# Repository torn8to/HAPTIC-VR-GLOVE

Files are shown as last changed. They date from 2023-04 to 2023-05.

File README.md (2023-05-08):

# Variable Haptic Feedback VR Gloves

We present the development of a haptic virtual reality (VR) glove with variable force feedback, electrotactile feedback, and finger tracking using a hall effect linear encoder and closed-loop control. The proposed glove consists of a custom-made linear encoder based on hall effect sensors to measure finger positions, and a closed-loop control system to provide variable force feedback. Additionally, the glove also attempts to incorporate electrotactile feedback to simulate the sensation of touch. Results show that the proposed glove is capable of providing realistic haptic feedback to users. We hope that this capability will improve the users sense of immersion and presence in virtual environments. Or allow for more intuitive control of various robotics systems. Overall, the proposed VR glove can serve as a valuable tool for a wide range of applications, including training simulations, gaming, and teleoperation.

<div id="cad_model" alingment="center">
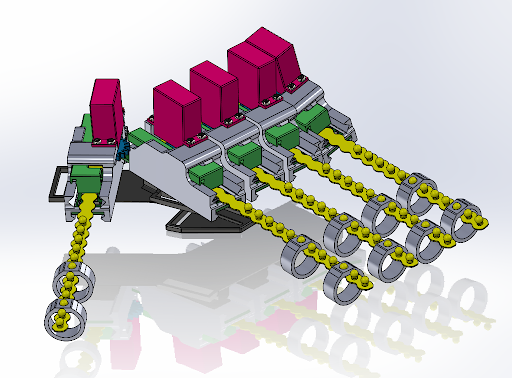
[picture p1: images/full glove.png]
   
</div>

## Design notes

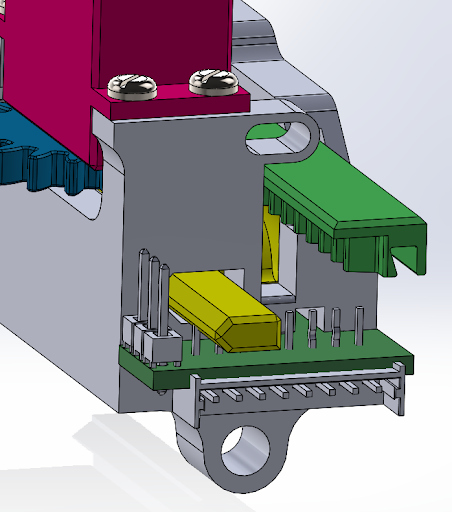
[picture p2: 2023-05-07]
images/back.png

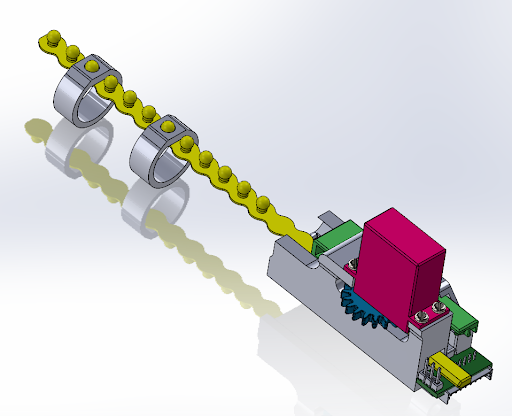
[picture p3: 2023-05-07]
images/full module.png

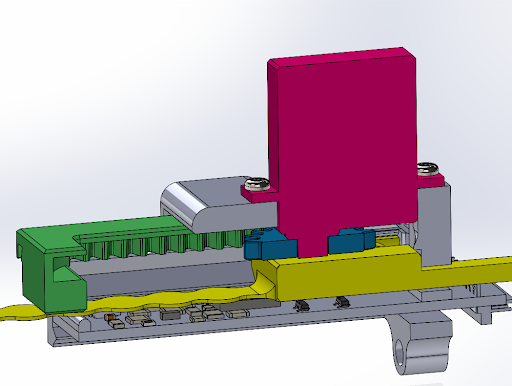
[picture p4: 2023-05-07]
images/cross-section not blocked.png

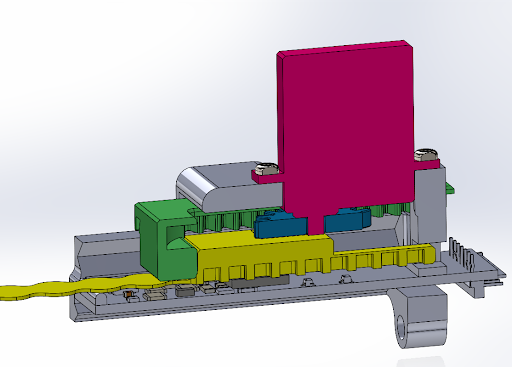
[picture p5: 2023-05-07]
images/cross-section blocked.png

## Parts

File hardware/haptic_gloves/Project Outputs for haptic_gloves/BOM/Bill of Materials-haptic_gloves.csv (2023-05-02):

comment | Designator | Footprint
Spacer, Round, 1/4 Inch O.D., 1/4 Inch Long, #8 Hole, Phenolic
KEYSTONE - 1048 - BATTERY HOLDER, 18650 LI-ION, 2CELL, SMD | B2
100 nf | C1, C3 | 2
330 nf | C2 | 1206_C
10 uf | C4 | 1206_C
1uf | C5, C7, C9, C10, C13 | 0805_C
4.7nf | C6, C8, C11, C12, C14 | 1206_C
 | J1, J2, J3, J4, J5, J6 | .1 1x8
THT Vertical Pin Header WR-PHD, Pitch 2.54 mm, Single Row, 20 pins | P1, P2 | 2.54mm to
Positive Voltage Regulator, 5V, 3-Pin TO-220 | U1 | 1
Fixed Low Drop Positive Voltage Regulator, 3.3V, 3-Pin TO-220 | U2 | 1
analog mux | U3, U9 | ssop-24
SENSOR CURRENT HALL | U4, U5, U6, U7, U8 | 8 soic

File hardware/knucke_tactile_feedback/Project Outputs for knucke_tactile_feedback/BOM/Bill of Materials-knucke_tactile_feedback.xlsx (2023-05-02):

comment | Designator | footprint
1uf | C1 | 0603_C
.1uf | C2, C3 | 0402_C
sMT connector | J2
TSW-103-07-L-S | P2 | .1 X 3
MMBT4403LT1G | Q1 | sot23-3
TNPU1206100RBZEN00 | R1, R2, R4, R5, R6, R8 | 1206_R
100 ohm resistor | R3, R7, R9 | 1210_R
20k resistor | R10 | 0805_R
10k resistor | R11 | 0805_R
10 ohm resistor | R12, R13 | 0805_R
hall effect sensor | U1, U2 | sot-23-3
HX711 | U3 | SOP-16

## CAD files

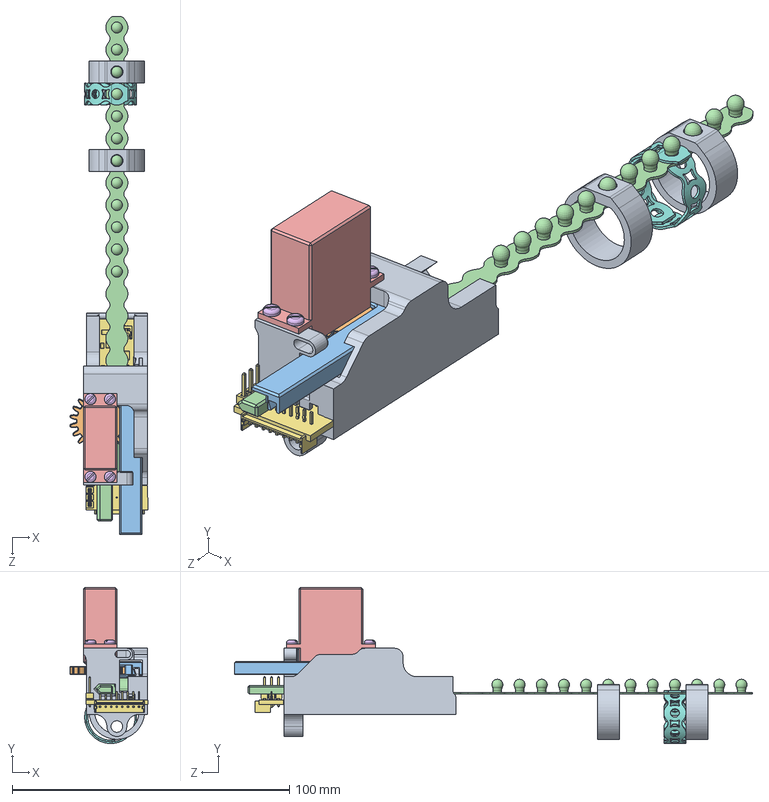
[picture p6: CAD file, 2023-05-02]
hardware/GloveAssembly/FingerModuleAssembly.SLDASM
28.1 x 56.2 x 186.8 mm
Base
ServoGear
ServoRackV2
Slider
AGFRC Micro Servo
pan head tapping screw_am x 4
FINGER_PCB
Ring8 x 2

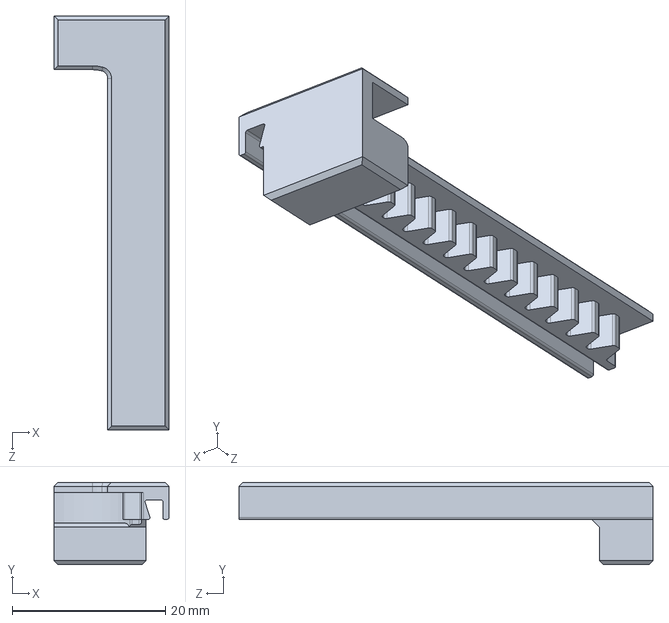
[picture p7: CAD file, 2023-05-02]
hardware/GloveAssembly/ServoRackV2.SLDPRT
15.0 x 10.7 x 54.0 mm

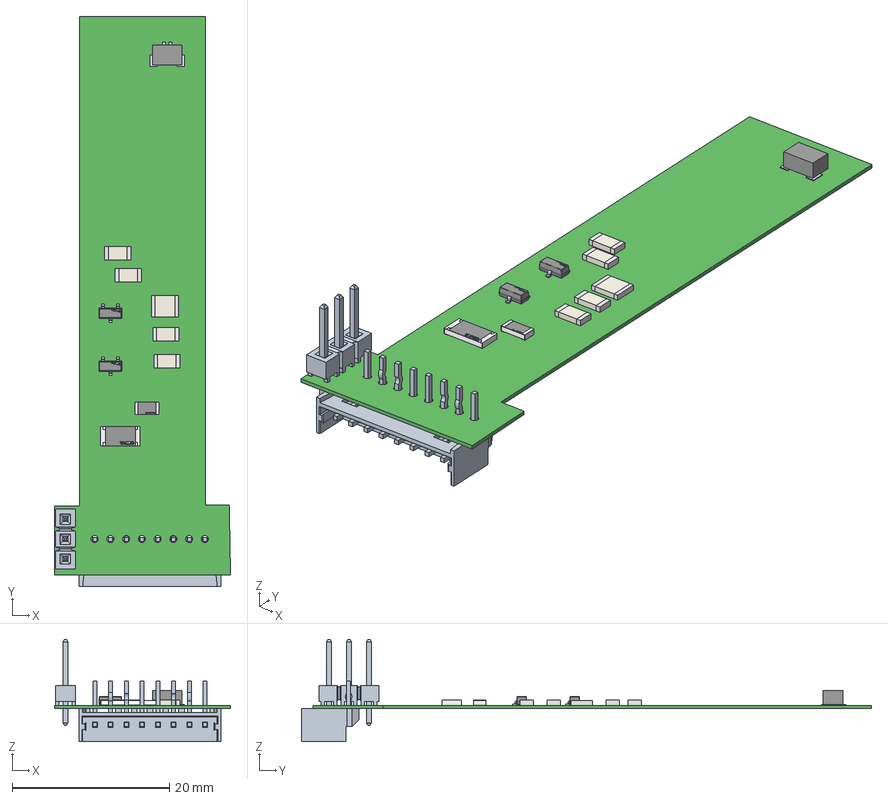
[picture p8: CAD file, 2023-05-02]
hardware/knucke_tactile_feedback/double_halleffect_corrected.step
22.4 x 72.5 x 13.0 mm
RC2010JK-071KL
Yageo
pins x 2
logo x 3
terminals
top
Pins
Extruded x 15
TSW-103-07-X-S

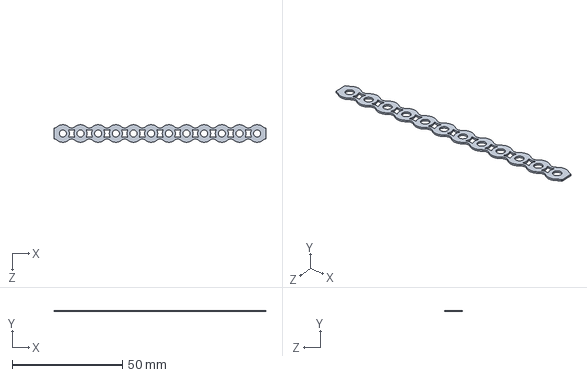
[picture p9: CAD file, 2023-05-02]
hardware/GloveAssembly/AdjustableRing.SLDPRT
96.0 x 0.6 x 8.00 mm

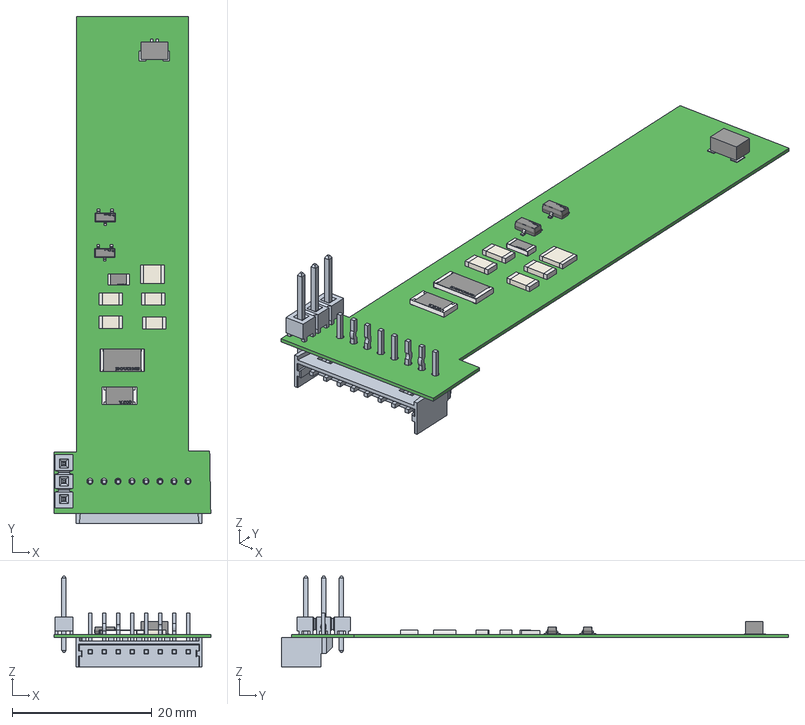
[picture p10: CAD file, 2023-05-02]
hardware/knucke_tactile_feedback/double_hall_effect.step
22.4 x 72.5 x 13.0 mm
RC2010JK-071KL
Yageo
pins x 2
logo x 4
terminals x 2
top x 2
Pins
Extruded x 15
TSW-103-07-X-S

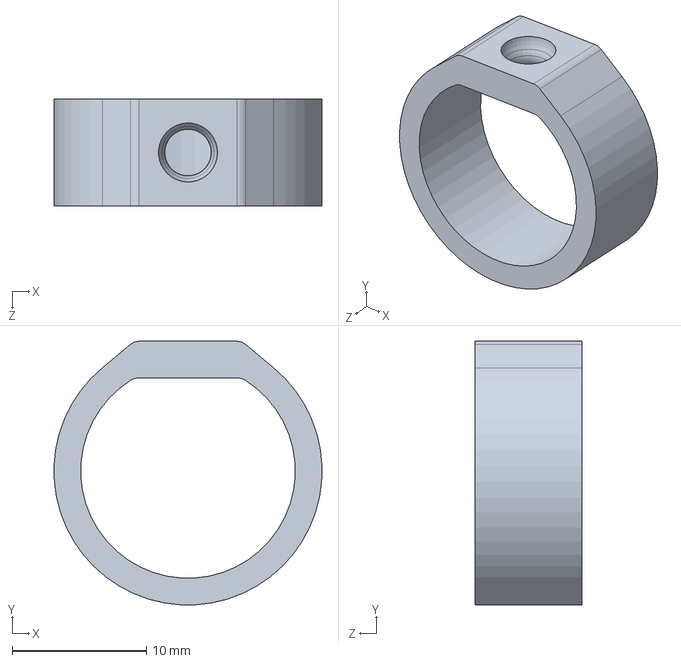
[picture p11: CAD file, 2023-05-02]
hardware/GloveAssembly/Ring8.SLDPRT
20.0 x 19.7 x 8.00 mm

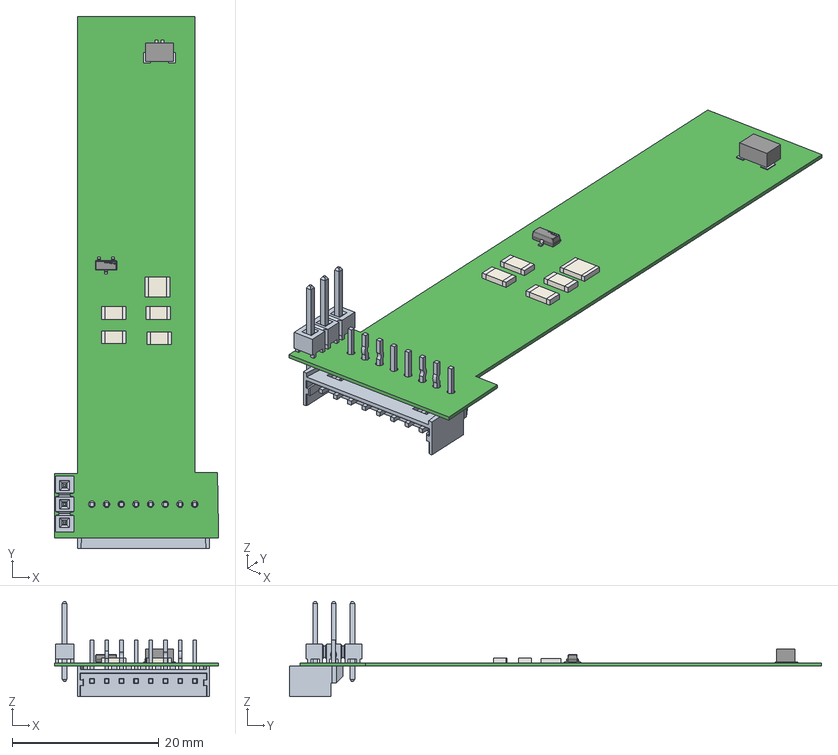
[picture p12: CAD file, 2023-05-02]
hardware/knucke_tactile_feedback/PCB1.step
22.4 x 72.5 x 13.0 mm
Pins
pins
logo
Extruded x 15
TSW-103-07-X-S

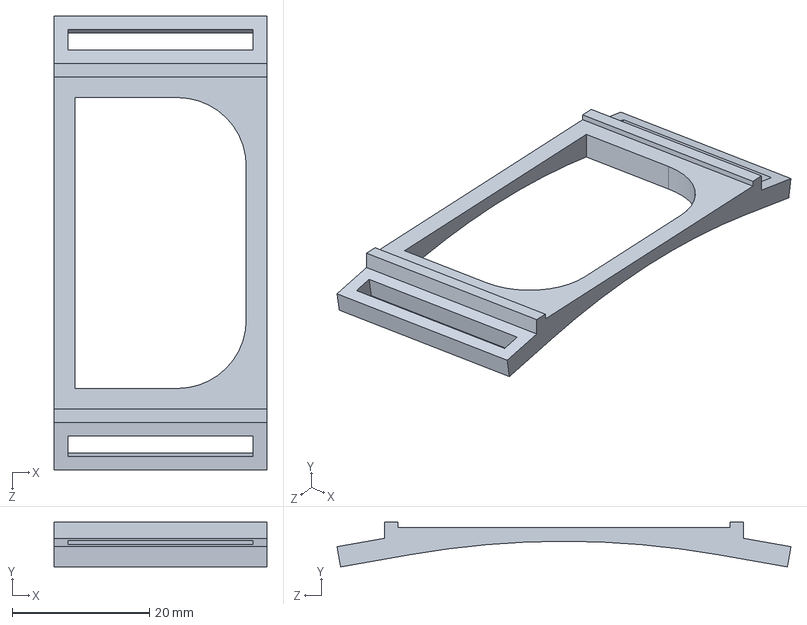
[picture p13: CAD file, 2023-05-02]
hardware/GloveAssembly/ArmBoardMount.SLDPRT
31.0 x 6.54 x 66.2 mm

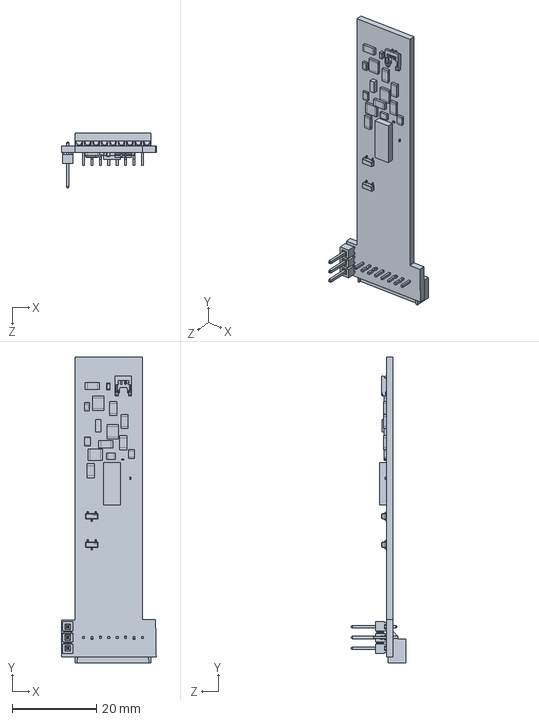
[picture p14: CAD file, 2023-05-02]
hardware/GloveAssembly/FINGER_PCB.SLDPRT
22.4 x 72.5 x 13.0 mm

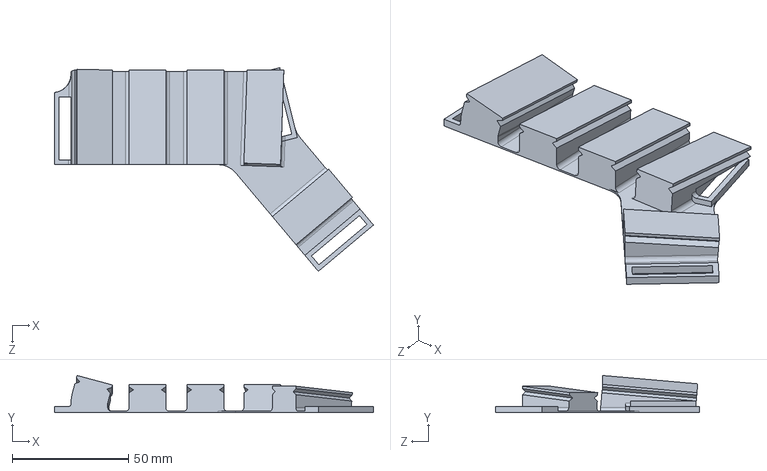
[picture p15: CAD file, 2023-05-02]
hardware/GloveAssembly/HandMount.SLDPRT
137.3 x 16.0 x 87.7 mm

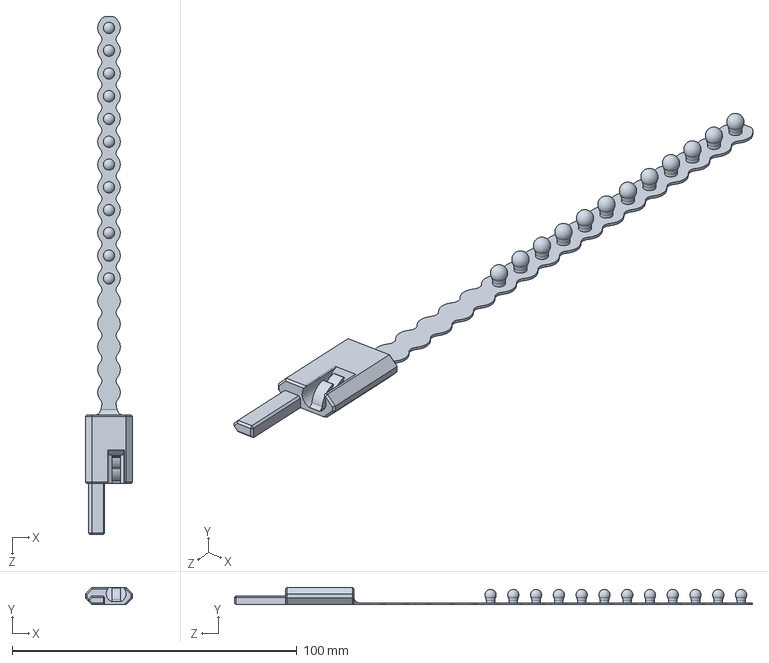
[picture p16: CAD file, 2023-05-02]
hardware/GloveAssembly/Slider.SLDPRT
16.6 x 6.00 x 181.9 mm

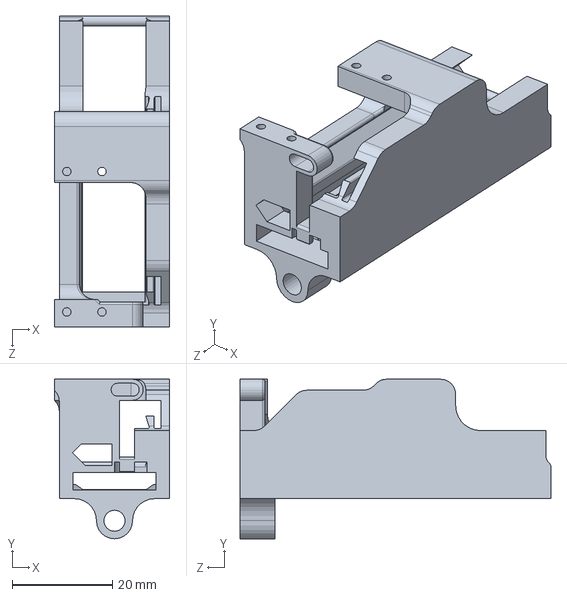
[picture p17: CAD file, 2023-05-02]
hardware/GloveAssembly/Base.SLDPRT
23.0 x 31.8 x 62.0 mm

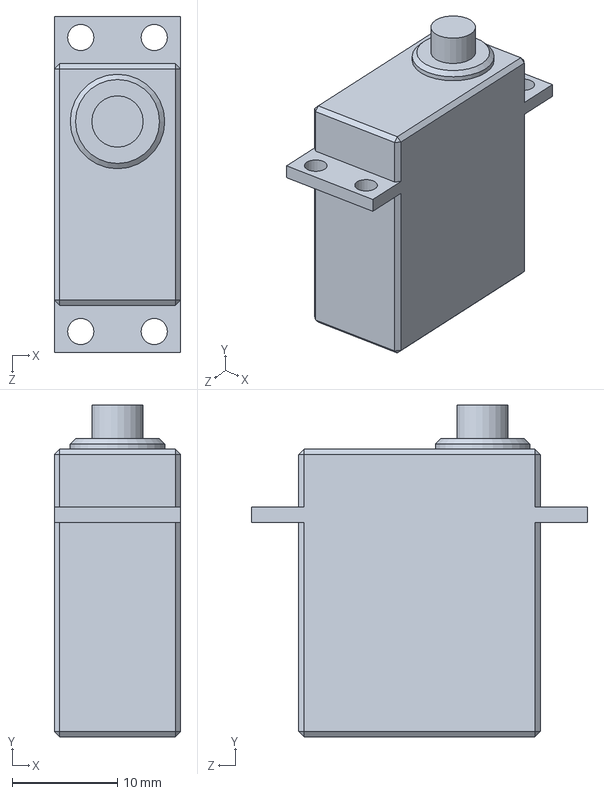
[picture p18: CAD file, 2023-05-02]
hardware/GloveAssembly/AGFRC Micro Servo.SLDPRT
12.0 x 31.6 x 32.0 mm

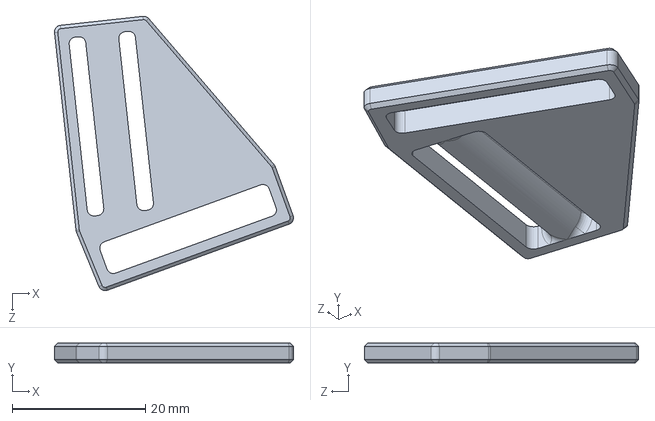
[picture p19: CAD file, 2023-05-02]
hardware/GloveAssembly/FrontHandClip.SLDPRT
35.9 x 3.00 x 41.2 mm

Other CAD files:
hardware/knucke_tactile_feedback/double_halleffect_placcement1.step
hardware/GloveAssembly/MasterSketch.SLDPRT
hardware/GloveAssembly/ServoGear.SLDPRT

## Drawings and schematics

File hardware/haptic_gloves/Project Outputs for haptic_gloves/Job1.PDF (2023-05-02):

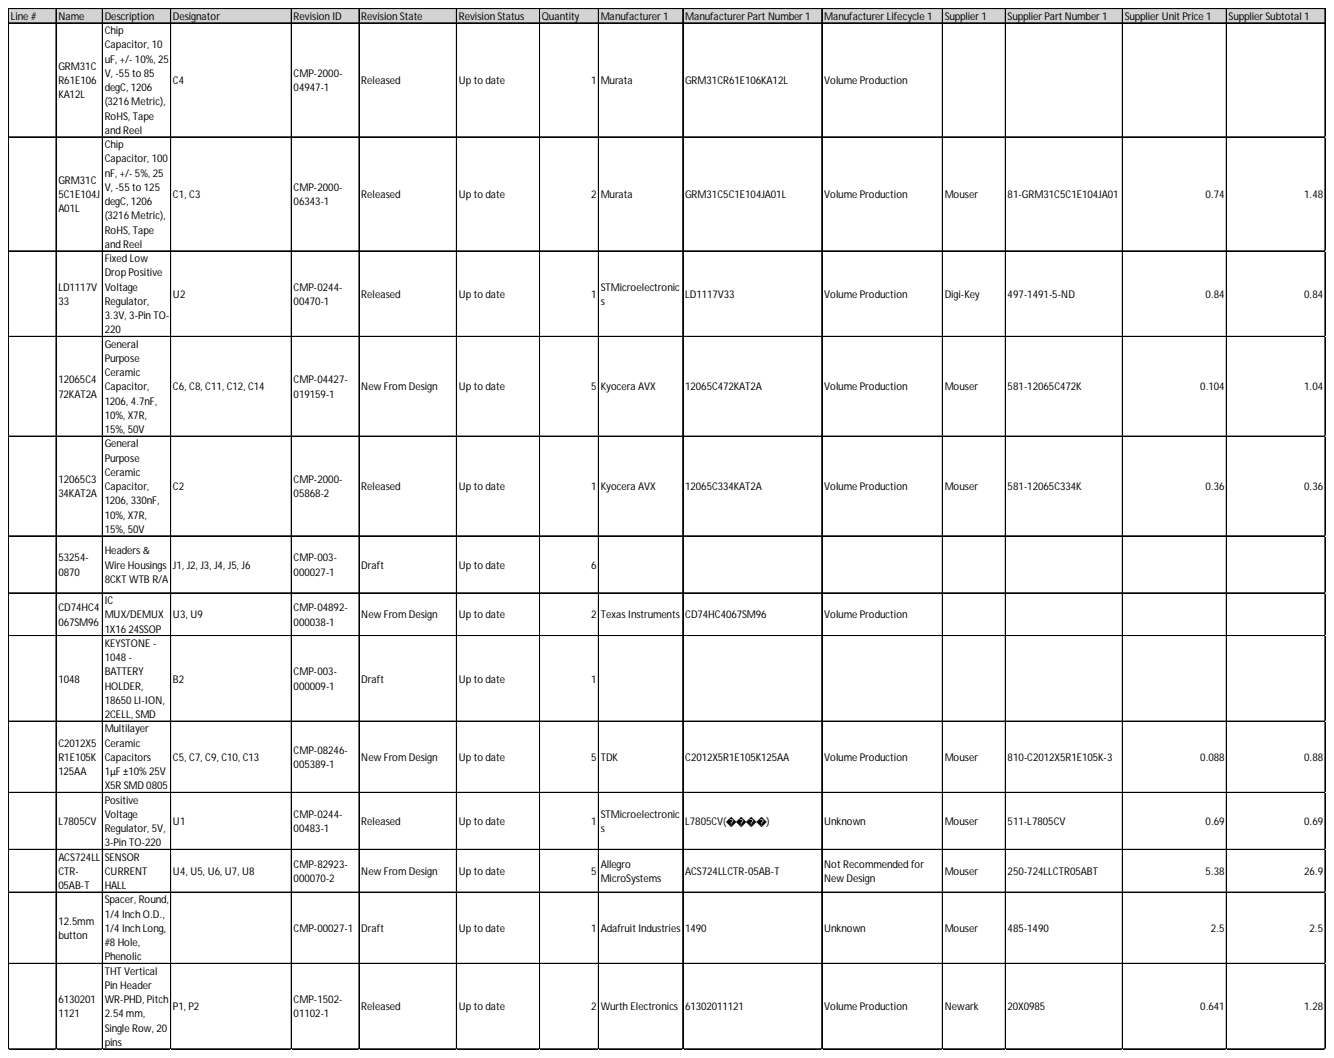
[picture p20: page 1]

Line # | Name | Description | Designator | Revision ID | Revision State | Revision Status | Quantity | Manufacturer 1 | Manufacturer Part Number 1 | Manufacturer Lifecycle 1 | Supplier 1 | Supplier Part Number 1 | Supplier Unit Price 1 | Supplier Subtotal 1

GRM31C R61E106 KA12L | Chip Capacitor, 10 uF, +/- 10%, 25 V, -55 to 85 degC, 1206 (3216 Metric), RoHS, Tape and Reel | C4 | CMP-2000-04947-1 | Released | Up to date | 1 | Murata | GRM31CR61E106KA12L | Volume Production

GRM31C 5C1E104J A01L | Chip Capacitor, 100 nF, +/- 5%, 25 V, -55 to 125 degC, 1206 (3216 Metric), RoHS, Tape and Reel | C1, C3 | CMP-2000-06343-1 | Released | Up to date | 2 Murata | | GRM31C5C1E104JA01L | Volume Production | Mouser | 81-GRM31C5C1E104JA01 | 0.74 | 1.48

LD1117V 33 | Fixed Low Drop Positive Voltage Regulator, 3.3V, 3-Pin TO-220 | U2 | CMP-0244-00470-1 | Released | Up to date | 1 | STMicroelectronic s | LD1117V33 | Volume Production | Digi-Key | 497-1491-5-ND | 0.84 | 0.84

12065C4 72KAT2A | General Purpose Ceramic Capacitor, 1206, 4.7nF, 10%, X7R, 15%, 50V | C6, C8, C11, C12, C14 | CMP-04427-019159-1 | New From Design | Up to date | 5 Kyocera AVX | | 12065C472KAT2A | Volume Production | Mouser | 581-12065C472K | 0.104 | 1.04

12065C3 34KAT2A | General Purpose Ceramic Capacitor, 1206, 330nF, 10%, X7R, 15%, 50V | C2 | CMP-2000-05868-2 | Released | Up to date | 1 | Kyocera AVX | 12065C334KAT2A | Volume Production | Mouser | 581-12065C334K | 0.36 | 0.36

53254-0870 | Headers & Wire Housings 8CKT WTB R/A | J1, J2, J3, J4, J5, J6 | CMP-003-000027-1 | Draft | Up to date | 6

CD74HC4 067SM96 | IC MUX/DEMUX 1X16 24SSOP | U3, U9 | CMP-04892-000038-1 | New From Design | Up to date | 2 Texas Instruments | | CD74HC4067SM96 | Volume Production

1048 | KEYSTONE -1048 -BATTERY HOLDER, 18650 LI-ION, 2CELL, SMD | B2 | CMP-003-000009-1 | Draft | Up to date | 1

C2012X5 R1E105K 125AA | Multilayer Ceramic Capacitors 1μF ±10% 25V X5R SMD 0805 | C5, C7, C9, C10, C13 | CMP-08246-005389-1 | New From Design | Up to date | 5 TDK | | C2012X5R1E105K125AA | Volume Production | Mouser | 810-C2012X5R1E105K-3 | 0.088 | 0.88

L7805CV | Positive Voltage Regulator, 5V, 3-Pin TO-220 | U1 | CMP-0244-00483-1 | Released | Up to date | 1 | STMicroelectronic s | L7805CV() | Unknown | Mouser | 511-L7805CV | 0.69 | 0.69

ACS724LL CTR-05AB-T | SENSOR CURRENT HALL | U4, U5, U6, U7, U8 | CMP-82923-000070-2 | New From Design | Up to date | 5 Allegro | MicroSystems | ACS724LLCTR-05AB-T | Not Recommended for New Design | Mouser | 250-724LLCTR05ABT | 5.38 | 26.9

12.5mm button | Spacer, Round, 1/4 Inch O.D., 1/4 Inch Long, #8 Hole, Phenolic | | CMP-00027-1 | Draft | Up to date | 1 | Adafruit Industries | 1490 | Unknown | Mouser | 485-1490 | 2.5 | 2.5

THT Vertical Pin Header WR-PHD, Pitch 2.54 mm, Single Row, 20 pins | P1, P2 | CMP-1502-01102-1 | Released | Up to date | 2 Wurth Electronics | | 61302011121 | Volume Production | Newark | 20X0985 | 0.641 | 1.28

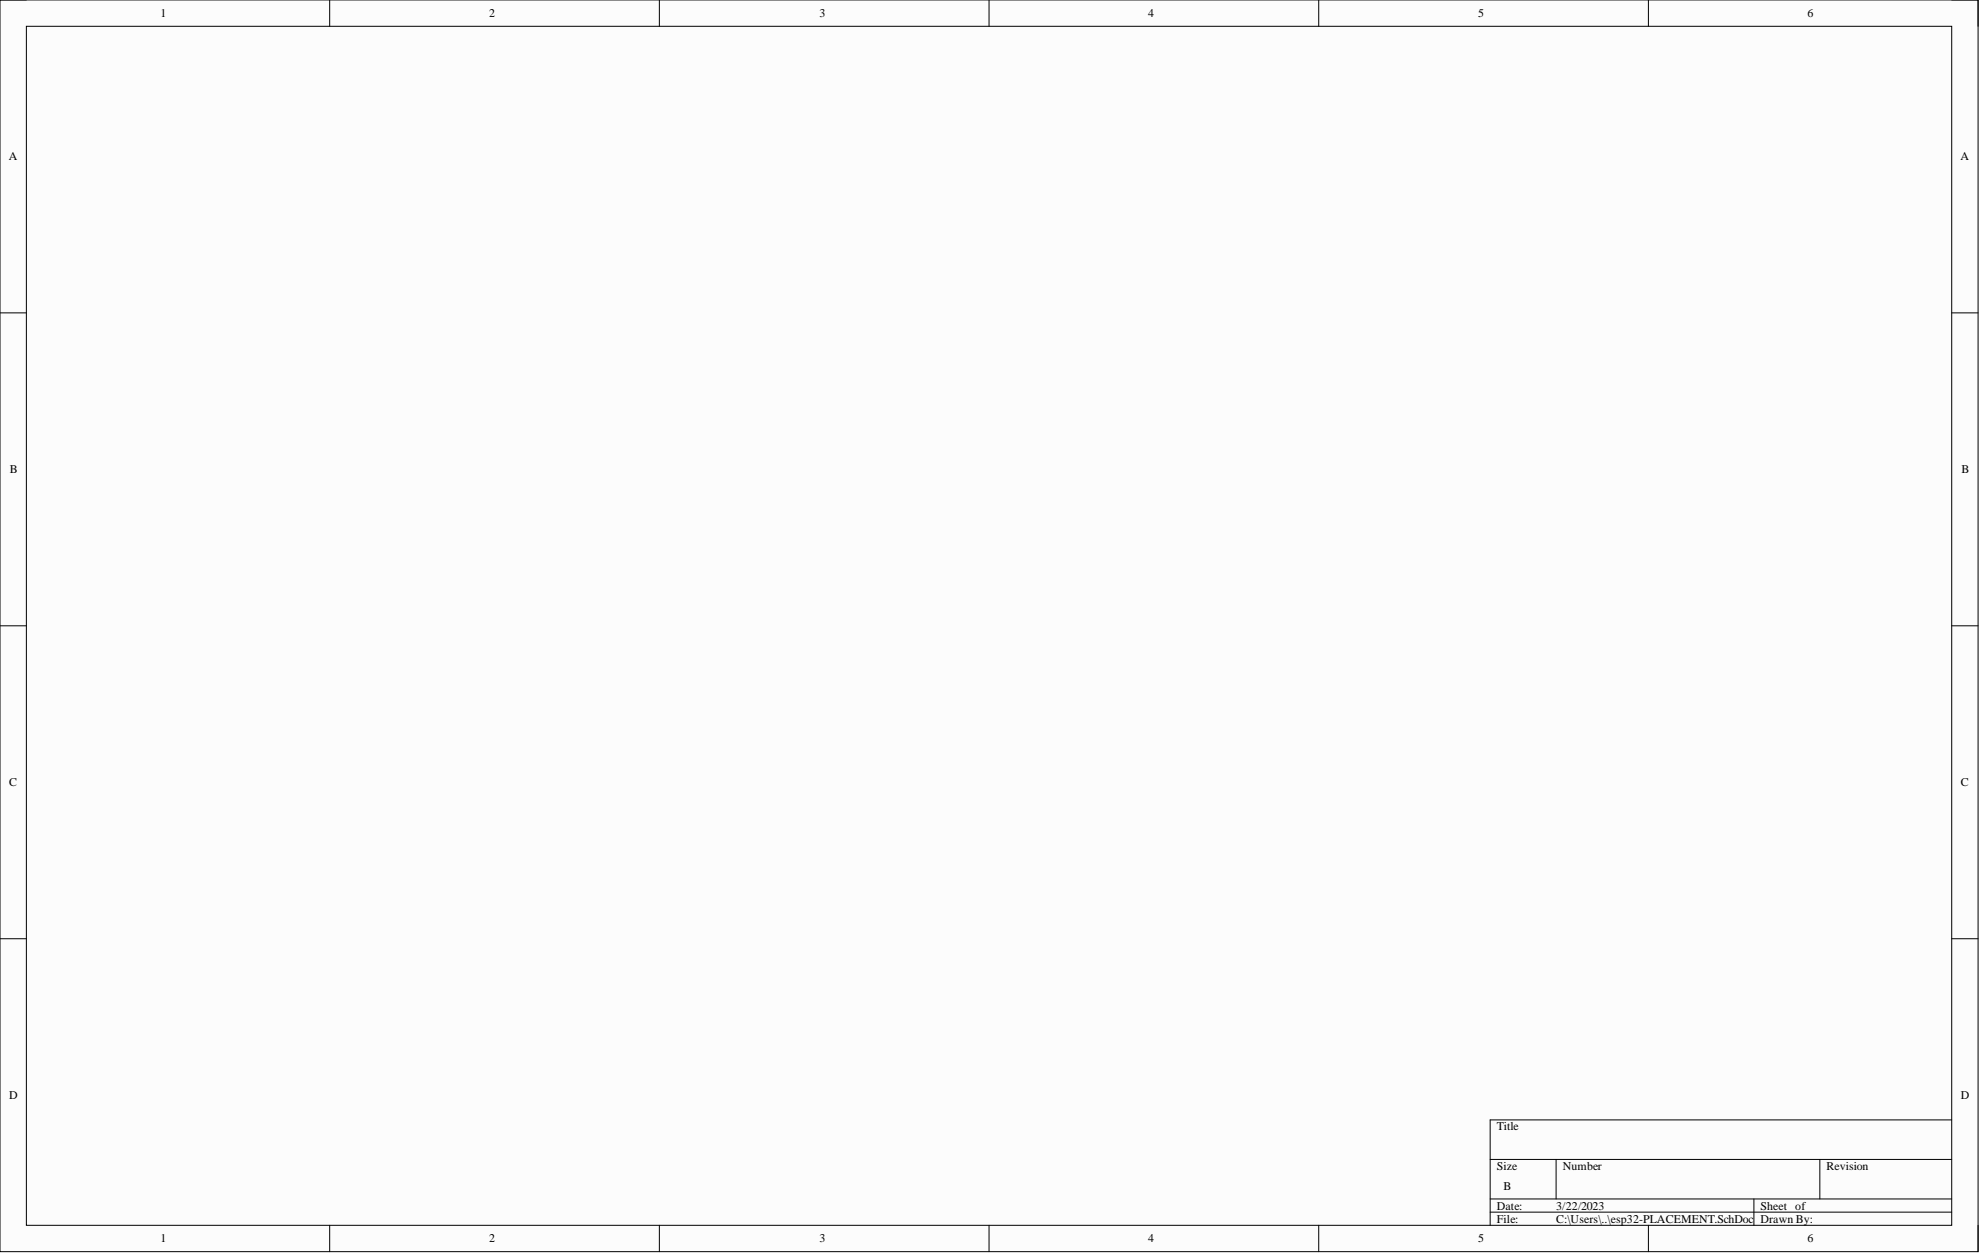
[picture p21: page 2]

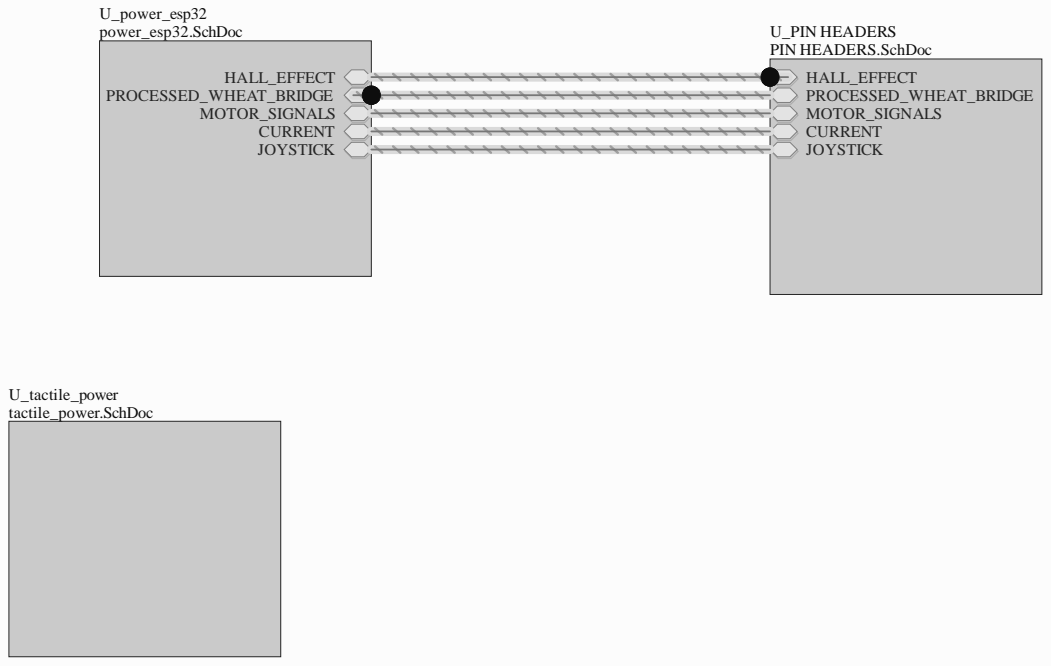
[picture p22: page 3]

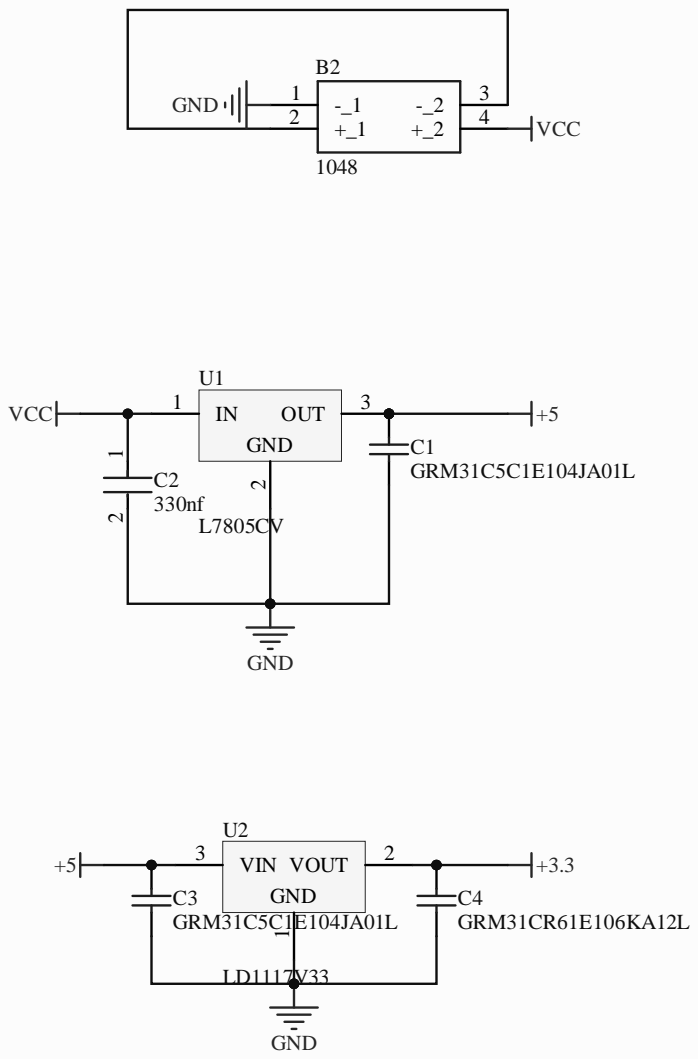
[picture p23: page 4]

tactile feeback power board w/ 5v and 3.3v voltage regulators

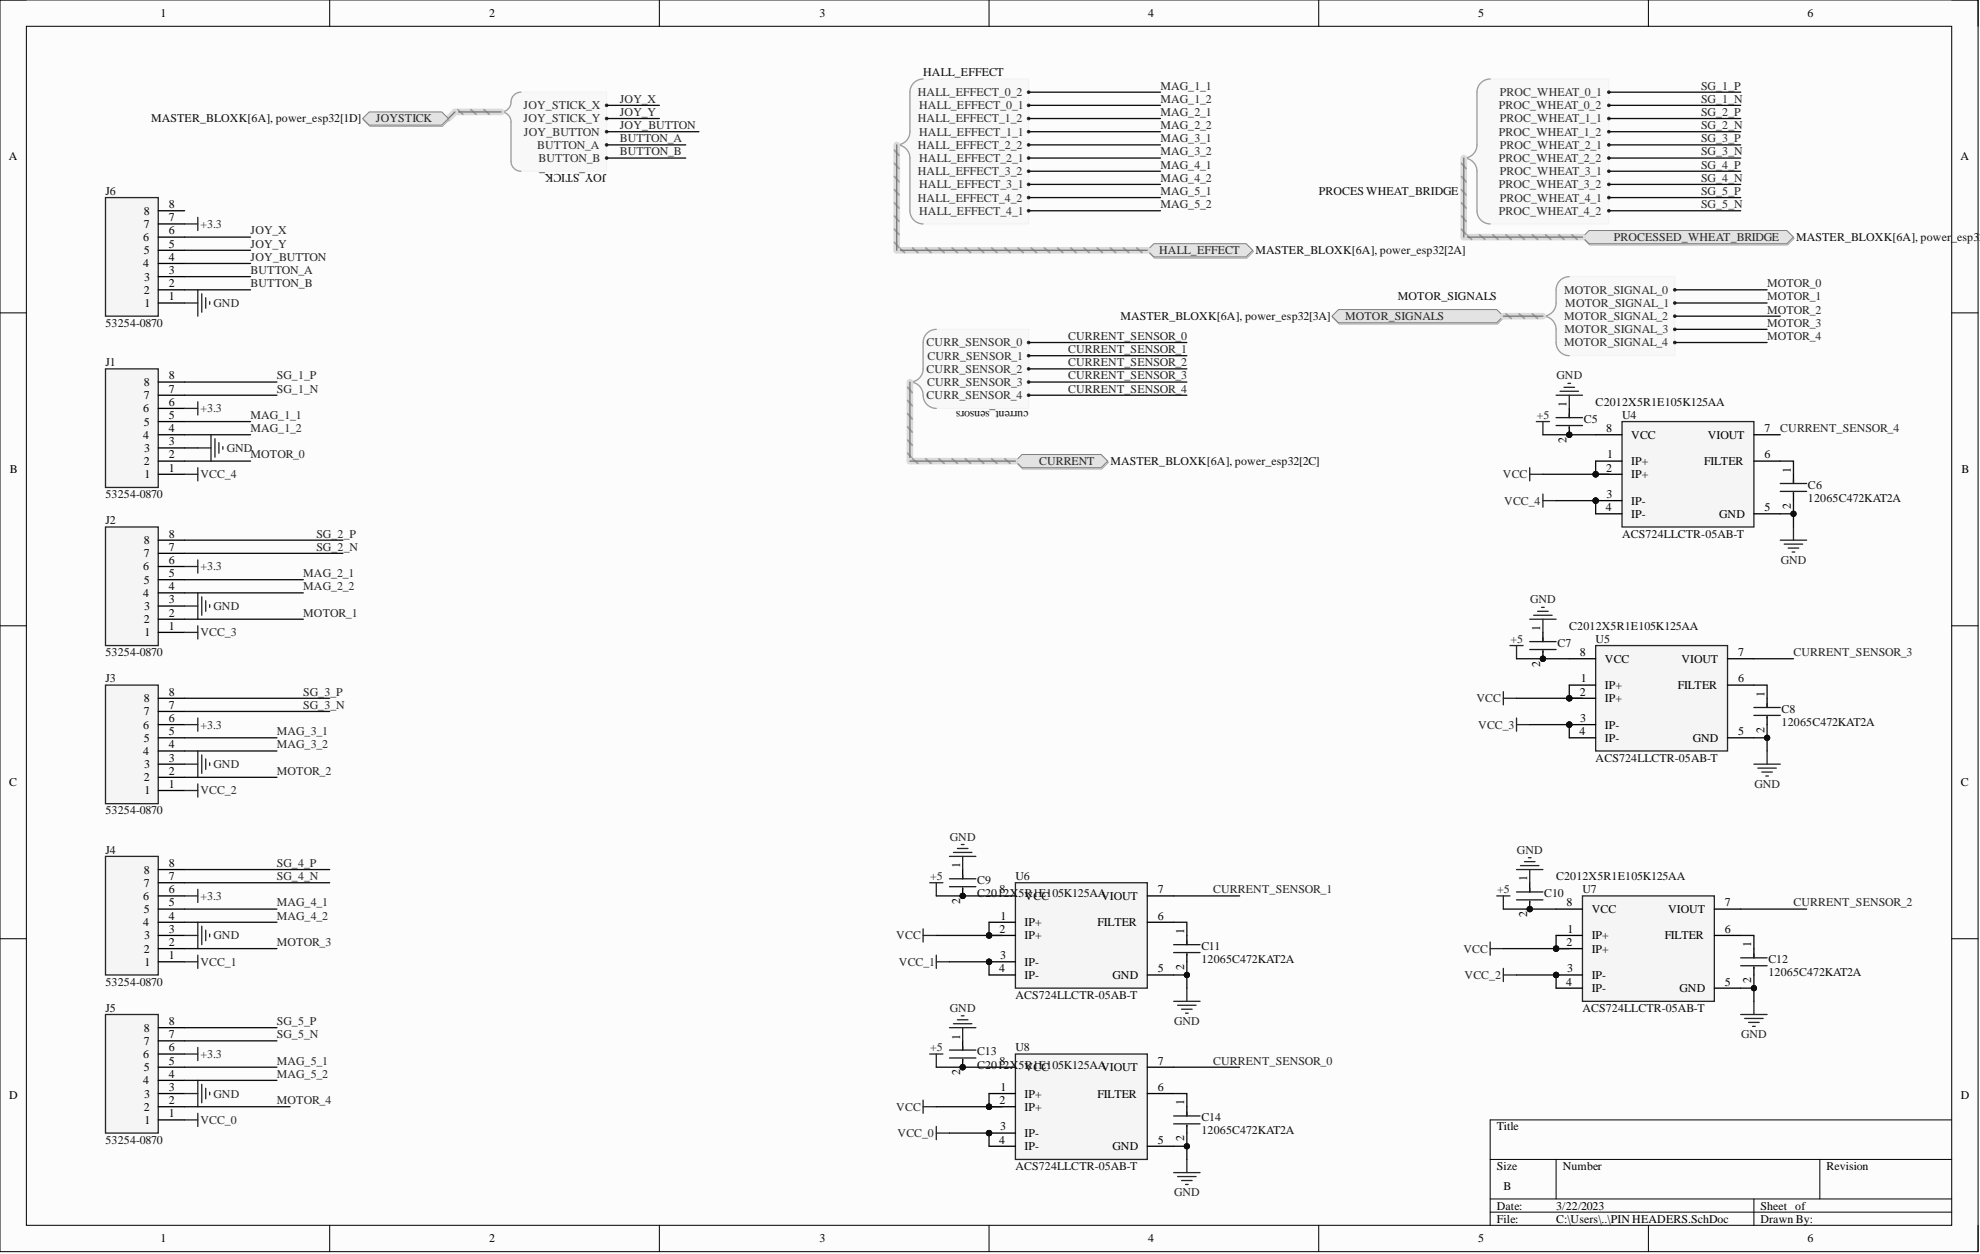
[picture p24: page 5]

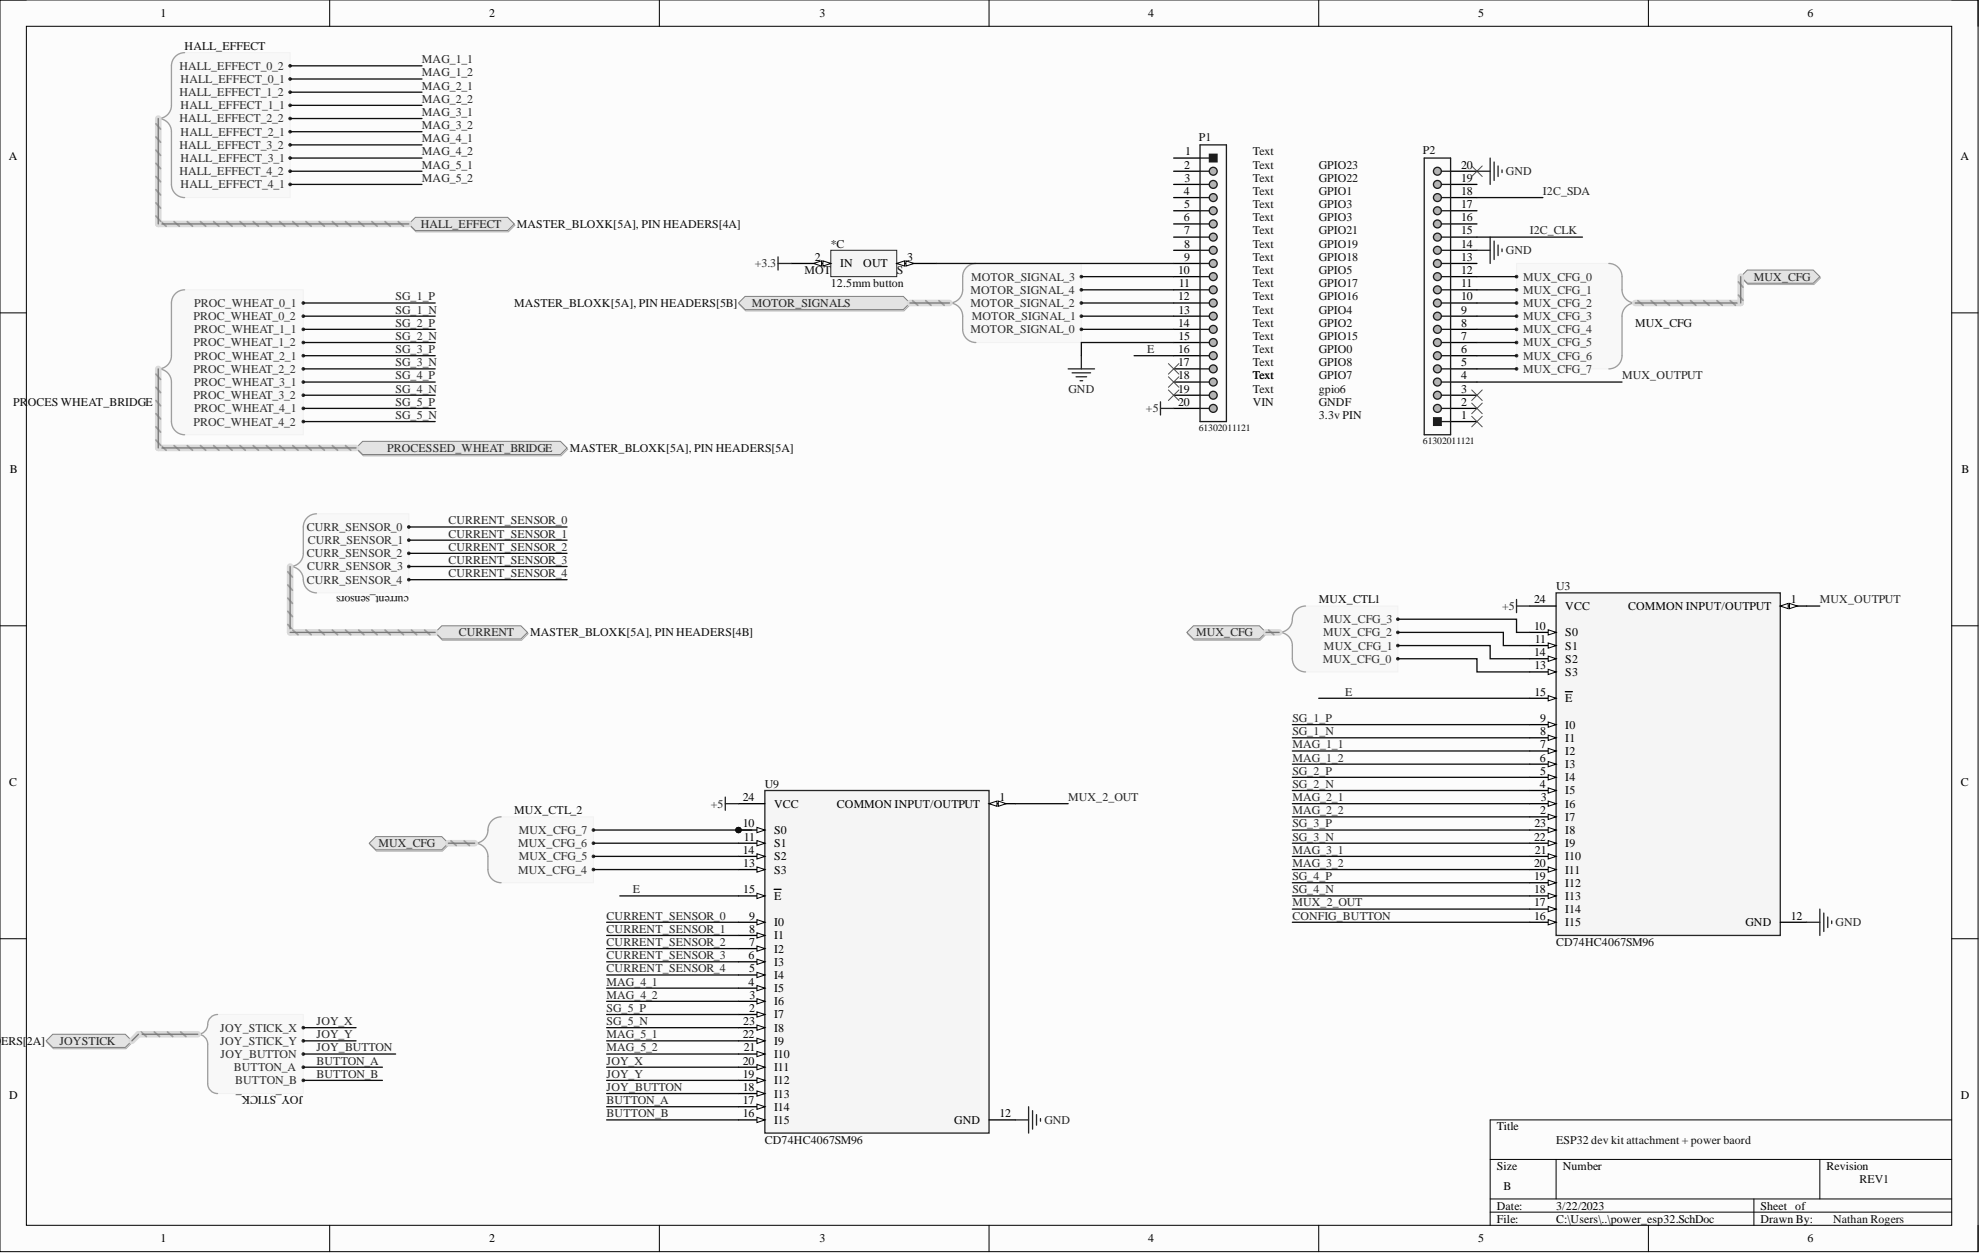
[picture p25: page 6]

S1 11
S2 14
S3 13

ESP32 dev kit attachment + power baord

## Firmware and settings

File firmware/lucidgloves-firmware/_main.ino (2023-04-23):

#include <mutex>
#define ALWAYS_CALIBRATING CALIBRATION_LOOPS == -1

#define CALIB_OVERRIDE false
#if USING_CALIB_PIN && COMMUNICATION == COMM_SERIAL && PIN_CALIB == 0 && !CALIB_OVERRIDE
  #error "You can't set your calibration pin to 0 over usb. You can calibrate with the BOOT button when using bluetooth only. Set CalibOverride to true to override this."
#endif

bool calibrate = false;
bool calibButton = false;
int* fingerPos = (int[]){0,0,0,0,0,0,0,0,0,0};

ICommunication* comm;

#if ESP32_DUAL_CORE_SET
//std::mutex fingerPosMutex;
ordered_lock* fingerPosLock = new ordered_lock();
TaskHandle_t Task1;
int threadLoops = 1;
int totalLocks = 0;
int lastMicros = 0;
int fullLoopTime = 0;
int fullLoopTotal = 0;
void getInputs(void* parameter){
    for(;;){
      fullLoopTime = micros() - lastMicros;
      fullLoopTotal += fullLoopTime;
      lastMicros = micros();
      {
        fingerPosLock->lock();
        totalLocks++;
        getFingerPositions(calibrate, calibButton); //Save finger positions in thread

        fingerPosLock->unlock();
      }
      threadLoops++;
      if (threadLoops%100 == 0){
        vTaskDelay(1); //keep watchdog fed
      }
      delayMicroseconds(1);
    }           
}
#endif

int loops = 0;
void setup() {

  pinMode(32, INPUT_PULLUP);
  
  #if COMMUNICATION == COMM_SERIAL
    comm = new SerialCommunication();
  #elif COMMUNICATION == COMM_BTSERIAL
    comm = new BTSerialCommunication();
  #endif  
  comm->start();

  setupInputs();

  #if USING_FORCE_FEEDBACK
    setupServoHaptics();  
  #endif
  
  #if ESP32_DUAL_CORE_SET
    xTaskCreatePinnedToCore(
      getInputs, /* Function to implement the task */
      "Get_Inputs", /* Name of the task */
      10000,  /* Stack size in words */
      NULL,  /* Task input parameter */
      tskIDLE_PRIORITY,  /* Priority of the task */
      &Task1,  /* Task handle. */
      0); /* Core where the task should run */
  #endif
}


int lastMainMicros = micros();
int mainMicros = 0;
int mainMicrosTotal = 0;
int mainloops = 1;

int target = 0;

bool latch = false;

void loop() {
  mainloops++;
  mainMicros = micros() - lastMainMicros;
  mainMicrosTotal += mainMicros;
  lastMainMicros = micros();

  if (!digitalRead(32)){
    if (!latch){
       target++;
       target %= 5;

       latch = true;
    }
  }
  else
    latch = false;
  
  if (comm->isOpen()){
    #if USING_CALIB_PIN
    calibButton = getButton(PIN_CALIB) != INVERT_CALIB;
    //Serial.println(getButton(PIN_CALIB));
    if (calibButton)
      loops = 0;
    #else
    calibButton = false;
    #endif


    //bool calibrate = false;
    if (loops < CALIBRATION_LOOPS || ALWAYS_CALIBRATING){
      calibrate = true;
      loops++;
    }
    else{
      calibrate = false;
    }

    #if !ESP32_DUAL_CORE_SET
      getFingerPositions(calibrate, calibButton);
    #endif
    bool joyButton = getButton(PIN_JOY_BTN) != INVERT_JOY;

    #if TRIGGER_GESTURE
    bool triggerButton = triggerGesture(fingerPos);
    #else
    bool triggerButton = getButton(PIN_TRIG_BTN) != INVERT_TRIGGER;
    #endif

    bool aButton = getButton(PIN_A_BTN) != INVERT_A;
    bool bButton = getButton(PIN_B_BTN) != INVERT_B;

    #if GRAB_GESTURE
    bool grabButton = grabGesture(fingerPos);
    #else
    bool grabButton = getButton(PIN_GRAB_BTN) != INVERT_GRAB;
    #endif

    #if PINCH_GESTURE
    bool pinchButton = pinchGesture(fingerPos);
    #else
    bool pinchButton = getButton(PIN_PNCH_BTN) != INVERT_PINCH;
    #endif

    int fingerPosCopy[10];
    int mutexTimeDone;
    bool menuButton = getButton(PIN_MENU_BTN) != INVERT_MENU;
    {
      #if ESP32_DUAL_CORE_SET
      int mutexTime = micros();
      //const std::lock_guard<std::mutex> lock(fingerPosMutex);
      fingerPosLock->lock();
      mutexTimeDone = micros()-mutexTime;
      #endif
      //memcpy(fingerPosCopy, fingerPos, sizeof(fingerPos));
      for (int i = 0; i < 10; i++){
        fingerPosCopy[i] = fingerPos[i];
      }
      #if ESP32_DUAL_CORE_SET
      fingerPosLock->unlock();
      #endif
      
    }

    comm->output(encode(fingerPosCopy, getJoyX(), getJoyY(), joyButton, triggerButton, aButton, bButton, grabButton, pinchButton, calibButton, menuButton));
    #if USING_FORCE_FEEDBACK
      char received[100];
      if (comm->readData(received)){
        int hapticLimits[5];
        //This check is a temporary hack to fix an issue with haptics on v0.5 of the driver, will make it more snobby code later
        if(String(received).length() >= 10) {
           decodeData(received, hapticLimits);
           writeServoHaptics(hapticLimits); 
        }
      }
    #endif
    delay(LOOP_TIME);
  }
}

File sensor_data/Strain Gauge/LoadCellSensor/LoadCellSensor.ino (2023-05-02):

/**
 * Complete project details at https://RandomNerdTutorials.com/arduino-load-cell-hx711/
 *
 * HX711 library for Arduino - example file
 * https://github.com/bogde/HX711
 *
 * MIT License
 * (c) 2018 Bogdan Necula
 *
**/

#include <Arduino.h>
#include "HX711.h"

// HX711 circuit wiring
const int LOADCELL_DOUT_PIN = 2;
const int LOADCELL_SCK_PIN = 3;

HX711 scale;

void setup() {
  Serial.begin(57600);

  scale.begin(LOADCELL_DOUT_PIN, LOADCELL_SCK_PIN);
            
  scale.set_scale(-5797.8571);
  //scale.set_scale(-471.497);                      // this value is obtained by calibrating the scale with known weights; see the README for details
  scale.tare();               // reset the scale to 0
}

void loop() {
  Serial.println(scale.get_units(), 1);

  delay(50);
}

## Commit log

2023-05-02 added folder for sensor analysis data/code, added linear hall effect sensor readings
    [Encoder Data.xlsx]
2023-05-02 added altium files for boards
    [Bill of Materials-haptic_gloves.csv, Bill of Materials-knucke_tactile_feedback.xlsx, MASTER_BLOXK.SchDoc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]
2023-05-02 cutting material
    [BearingRetainer_v1.2.STL, ESP32_Wroom_Holder_Desoldered_JST.STL, EndRing_v1.2_13mm.STL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]
2023-05-02 adding opengloves driver as submodule
2023-05-02 fixed sensor data organization
    [straingaugedata.xlsx]
